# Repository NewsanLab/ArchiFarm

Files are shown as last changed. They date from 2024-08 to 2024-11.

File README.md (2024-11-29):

# 🌱 Proyecto de Cultivo en tu propio Smart Indoor
Este proyecto está diseñado para que cualquier persona pueda crear un sistema automatizado de cultivo indoor para lechugas. Usando tecnología accesible, hemos desarrollado un sistema que permite monitorear y optimizar el crecimiento de las plantas en interiores, subiendo los datos adquiridos a la plataforma Thingspeak para su análisis y seguimiento.
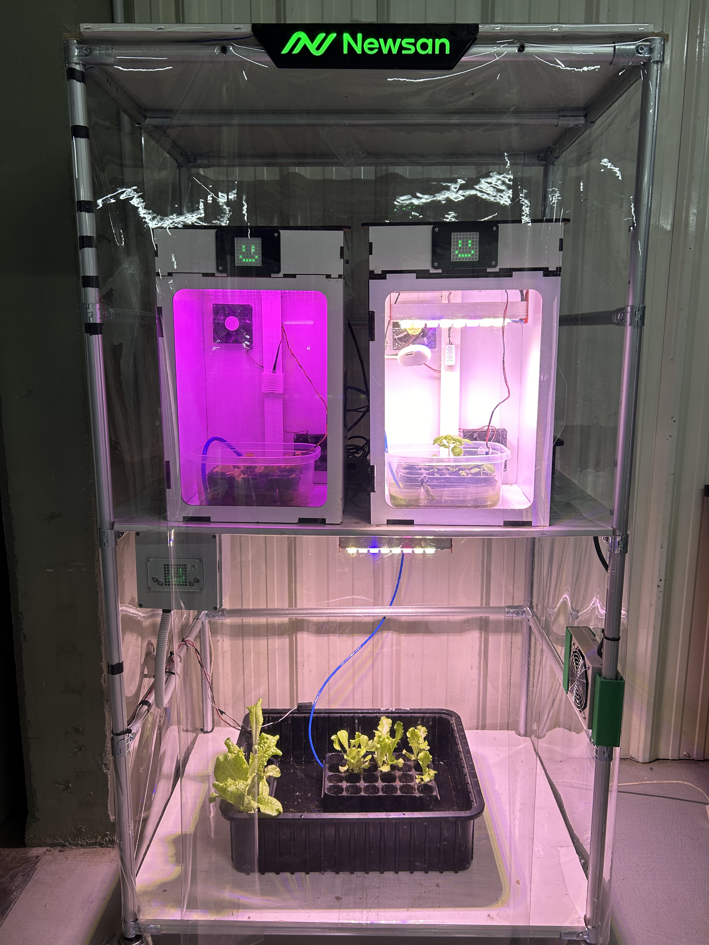
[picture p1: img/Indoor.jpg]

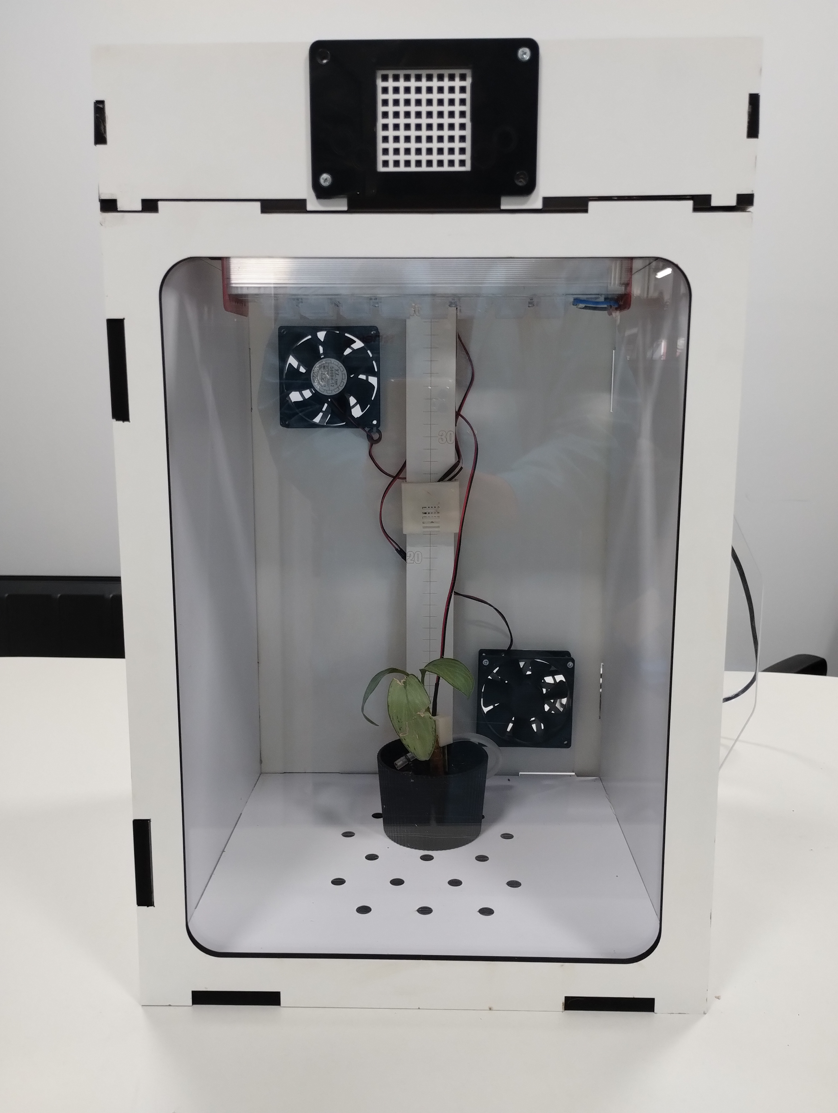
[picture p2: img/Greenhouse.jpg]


# 📖 Descripción
El proyecto de cultivo indoor de lechugas se centra en el desarrollo de un sistema inteligente que controla automáticamente las condiciones de crecimiento de las plantas. Este sistema incluye un conjunto de sensores y actuadores conectados a una placa de control diseñada específicamente para este propósito, llamada Archi Farm Beta. Con este sistema, es posible mantener las condiciones óptimas de luz, temperatura, humedad y riego para asegurar un crecimiento saludable de las lechugas.


# 🔧 Especificaciones Técnicas
- Placa Controladora: Archi Farm Beta, compatible con el microcontrolador Archi y Arduino Uno.
- Sensores Integrados: Sensor de humedad de suelo, sensor de temperatura y humedad ambiental.
- Actuadores: Luces LED Full Spectrum HPR16BOSV1, bomba de agua sumergible 600L/H 8W, coolers 220V AC.
- Alimentación: 220V AC para los actuadores principales y 5V DC para la placa de control y sensores.
- Conectividad: Capacidad de subir datos a Thingspeak mediante conexión Wi-Fi.
- Relés de Estado Sólido: Control de actuadores mediante salidas de relés.

# ⚙️ Esquema de Conexiones
A continuación se presenta el esquema de conexiones del sistema. Este esquema muestra cómo se conectan los sensores, actuadores y la placa controladora Archi Farm Beta.
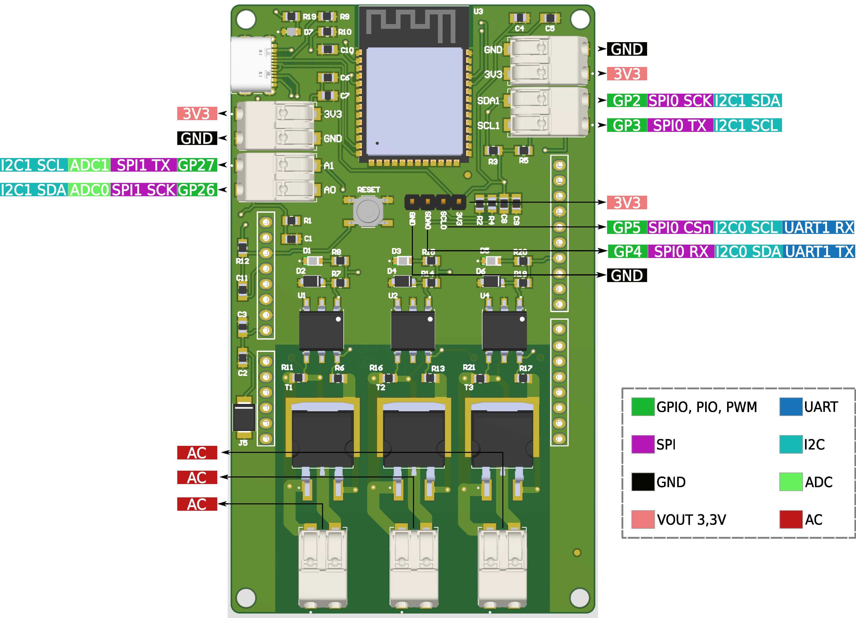
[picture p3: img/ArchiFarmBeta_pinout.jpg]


# 📜 Historia del Proyecto
El proyecto comenzó con la idea de desarrollar un método eficiente y controlado para cultivar lechugas en interiores, especialmente en áreas urbanas donde el espacio y las condiciones climáticas pueden ser limitantes. Tras varias iteraciones, logramos optimizar un sistema que no solo regula el ambiente de las plantas, sino que también permite subir los datos en tiempo real a una plataforma en la nube. De esta manera, cualquier persona puede monitorear y ajustar las condiciones de su cultivo desde cualquier lugar.

La primera versión del sistema utilizaba un método más simple para controlar la humedad y la luz, pero con el tiempo, se incorporaron tecnologías más avanzadas como la conexión a internet y el uso de la placa Archi Farm Beta, que mejoraron significativamente el rendimiento y la eficiencia del cultivo.

# 🗒 Historial de Cambios
v1.0: Primera versión del sistema, basada en un control manual de luces, riego y ventilacion. Tambien incluye conectividad a internet y puertos libre de proposito general.

# 🔗 Links Útiles
- [Archi](https://archikids.com.ar/)
- [Thingspeak](https://thingspeak.com/)

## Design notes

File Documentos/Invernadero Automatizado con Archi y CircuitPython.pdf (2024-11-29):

Invernadero Automatizado con Archi y CircuitPython ¡Bienvenidos al emocionante mundo de la automatización de invernaderos con tecnología! En este proyecto, exploramos cómo construir un invernadero automatizado que utiliza el potente microcontrolador Archi y el versátil entorno de programación CircuitPython. Este invernadero inteligente es capaz de monitorear y controlar las condiciones ambientales para garantizar el crecimiento saludable de las plantas.
Características del Proyecto:

Componentes:

Funcionamiento:

1. Control de Luz LED de Espectro Completo: Una luz LED de espectro completo proporciona a las plantas la iluminación adecuada para su crecimiento.
2. Riego Automático: Una bomba de agua automatizada se encarga de regar las plantas en el momento adecuado.
3. Regulación de Temperatura: Dos ventiladores (coolers) mantienen la temperatura dentro del invernadero en niveles óptimos.

Microcontrolador Archi
Placa de desarrollo Archi Farm Beta
Fuente de Alimentación 5V
SHT30: Sensor de Humedad y Temperatura del Ambiente Sensor Capacitivo de Humedad de Suelo (CSMS)
RTC (real time clock) DS3231
2 ventiladores “cooler” de 220v
Bomba de agua sumergible 220v
Luz LED Full Spectrum 220v
1. Los sensores SHT30 y CSMS están colocados en una carcasa impresa en 3D. El sensor SHT30 está conectado a los GP4 (I2C0 SDA) y GP5 (I2C0 SCL) de Archi, mientras que el CSMS está conectado al pin A0.
2. El microcontrolador Archi contiene una matriz led y botones (entre otras cosas). Dichos botones son usados para mostrar por pantalla los datos de humedad de ambiente, temperatura y humedad de suelo porcentual.
3. Se utiliza también un RTC el cual tiene la hora guardada, de manera de controlar la luz durante un rango de hora desde inicio hasta apagado. El RTC usa una pila cr2032 la cual permite guardar los datos de segundos, minutos,

Además, cuenta con un ESP32 S3 WROOM 1 el cual recibe los datos desde Archi y los publica en Thingspeak. Para la conexión se usaron los pines GP16 (UART0 TX) y GP17 (UART0 RX). La comunicación UART permite el envío y recepción de datos entre Archi y ESP32. Para la programación de la ESP32 se conecta usb tipo c en el conector al lado del Esp32

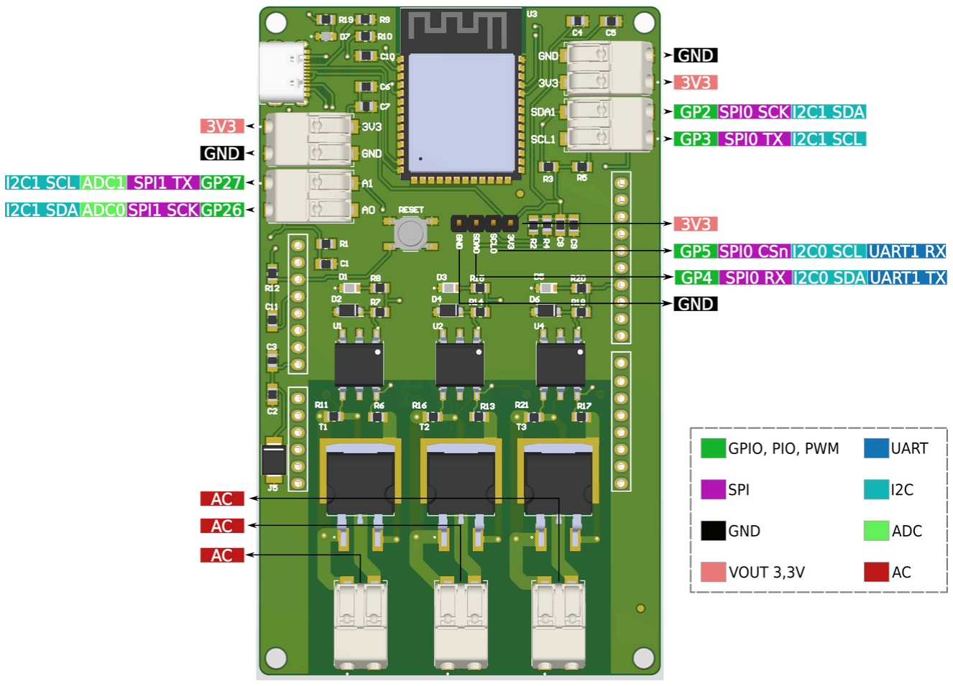
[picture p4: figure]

Finalmente, conectamos a nuestra pc y programamos el archivo “Code_ESP32_WROOM1” usando el Arduino IDE.
No olvides introducir en nombre de la red wifi, contraseña y la API de Thingspeak en código de la ESP32, de contrario no funcionará.
Instrucciones:

hora, día, mes y año. El RTC está conectados a los pines GP2 (I2C1 SDA) y GP3 (I2C1 SCL) de Archi, pero puedes usar los mismos pines que el sensor SHT30.
4. La placa de desarrollo Archi Farm Beta contiene 3 relés de estado sólido para controlar actuadores de 220v de AC. También cuenta con leds que se encienden y apagan junto con cada relé. Cada relé está conectado con los pines GP13, GP14 y GP15.
1. Clona o descarga este repositorio en tu computadora.
2. Configura el entorno de desarrollo para el microcontrolador Archi y CircuitPython siguiendo las instrucciones proporcionadas en el README.

Imágenes y Esquemas:
Puedes encontrar imágenes del invernadero y de los componentes en la carpeta "img" de este repositorio.
Notas de Seguridad:

¡Ahora estás listo para sumergirte en el emocionante proyecto de tu invernadero automatizado con Archi y CircuitPython! Recuerda, este tutorial está diseñado para ser amigable para los principiantes y está pensado para inspirar el aprendizaje y la exploración. ¡Diviértete y disfruta del proceso de construcción y aprendizaje!

3. Ve a https://archikids.com.ar y presiona el boton Code Editor.
4. Carga el código en el Archi usando el archivo de código fuente en formato CircuitPython (code.py). No olvides cargar las librerías en la carpeta lib.
5. Coloca los sensores en la carcasa impresa y posiciónalos en el invernadero.
6. Conecta los dispositivos controlados (ventiladores, bomba, luz) al módulo de relés.
7. Conecta la fuente de alimentación y enciende el invernadero automatizado.

Al tratar con dispositivos eléctricos de alto voltaje, asegúrate de tomar todas las precauciones de seguridad necesarias.
Mantén el invernadero en un lugar seguro y bien ventilado.

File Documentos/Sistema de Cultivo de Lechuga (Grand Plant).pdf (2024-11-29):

Sistema de Cultivo de Lechuga (Grand Plant) Materiales Utilizados:

Como hacer un Plantín:
Para preparar el sustrato, primero es necesario humedecerlo y removerlo bien. Esto asegura que el aire circule dentro de la tierra, lo que es esencial para el desarrollo de las raíces. Una vez listo, se coloca el sustrato en los speedlings, dejando unos 5mm libres en la parte superior para colocar las semillas. Debes poner dos semillas en cada hueco y luego cubrirlas con una fina capa de tierra. Es fundamental rociar agua para mantener la humedad constante en el sustrato. Una vez que el speedling esté listo, se debe colocar en un recipiente con agua previamente preparada con soluciones hidropónicas. La preparación del agua dependerá de las instrucciones de cada nutriente que utilices. Ahora, coloca el sensor de humedad de suelo en la tierra para monitorear la humedad de manera constante.
Durante nuestros primeros ensayos, cubrimos los semilleros con una bolsa de plástico para aumentar la humedad. Sin embargo, la luz que llegaba a los plantines hacía que se estiraran demasiado, lo que no es beneficioso para el cultivo de lechugas. Luego, descubrimos que era mejor privar a los plantines de luz en esta etapa inicial, aunque el crecimiento seguía siendo algo lento.

Luz HPR16BOSV1 con disipador Ventiladores 220V AC
Bomba de Agua Sumergible 600L/H 8W Sustrato
Speedlings (bandejas para germinación)
Recipiente
Nutrientes para hidroponía Minamot: ROOTDROP, FULLDROP A y FULLDROP B

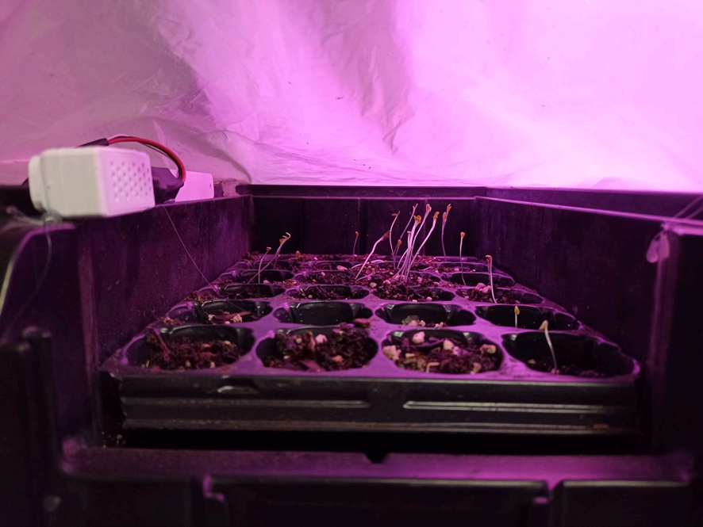
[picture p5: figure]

Posteriormente, decidimos colocar los plantines desde el primer día en un indoor equipado con luces HPR16BOSV1. Aunque la humedad ambiental no era tan alta como en el experimento anterior, estas luces, que incluyen diferentes tipos de LEDs, permitieron un crecimiento más equilibrado de los plantines. Es importante mencionar que mantuvimos una distancia de 25 cm entre las luces y los plantines. Esta distancia es crucial, ya que si las luces están demasiado lejos, las lechugas tienden a estirarse, lo que no es ideal para su desarrollo.
Condiciones del Ensayo (para Lechugas):

18 horas de luz por día
Rango de temperaturas entre 18°C y 28°C
Humedad ambiental mayor al 40%

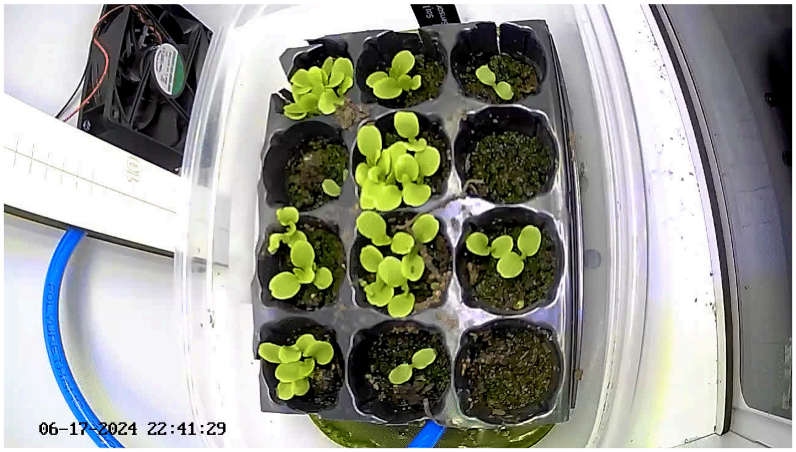
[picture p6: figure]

Después de dos o tres semanas, es necesario trasladar los plantines a un espacio más grande y aumentar la distancia entre las luces y las plantas a aproximadamente 1 metro. Este cambio es vital para que las plantas sigan creciendo de manera adecuada. Si las plantas permanecen en un espacio pequeño y con la luz demasiado cerca, su crecimiento se verá limitado.
En la imagen, se pueden ver lechugas de distintos tamaños. Las lechugas más grandes fueron trasladadas a un espacio más amplio una semana antes, lo que les permitió crecer más rápidamente. Por otro lado, las plantas más pequeñas permanecieron en el espacio reducido durante esa semana adicional, lo que limitó su crecimiento.

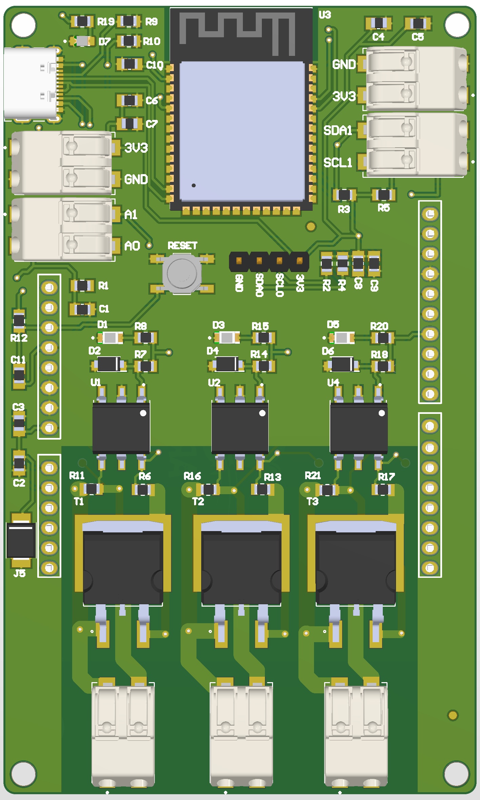
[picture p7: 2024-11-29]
Hardware/Archi_Farm_Beta.jpg

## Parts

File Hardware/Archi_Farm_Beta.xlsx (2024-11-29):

PartType | Description | Value | Designator | Package | Quantity
CC0805JPNPO9BN102 | CAP CER 1000PF 50V C0G/NPO 2012M | 1000pF | C11 | 2012M | 1
CRCW0805270RFKEAC | 270 Ohms ±1% 0.125W, 1/8W Chip Resistor 2012M | 270ohms | R8, R15, R19, R20 | 2012M | 4
CRCW0805220RFKEBC | 220 Ohms ±1% 0.125W, 1/8W Chip Resistor 2012M | 220ohms | R6, R7, R13, R14, R17, R18 | 2012M | 6
CRCW080556R0FKEAC | 56 Ohms ±1% 0.125W, 1/8W Chip Resistor 2012M | 56ohms | R11, R16, R21 | 2012M | 3
CC0805JPNPO9BN470 | 47 pF ±5% 50V Ceramic Capacitor C0G, NP0 2012M | 47pF | C1 | 2012M | 1
CC0805ZKY5V5BB106 | CAP CER 10UF 6.3V Y5V 2012M | 10uF | C2, C4, C6, C8, C10 | 2012M | 5
CRCW080510K0FKEA | 10 kOhms ±1% 0.125W, 1/8W Chip Resistor 2012M | 10kohms | R2, R3, R4, R5 | 2012M | 4
CRCW08055K00JNTA | 5 kOhms ±5% 0.125W, 1/8W Chip Resistor 2012M | 5kohms | R9, R10 | 2012M | 2
CRCW08051K00FKEA | RES SMD 1K OHM 1% 1/8W 2012M | 1kohms | R1, R12 | 2012M | 2
CC0805KRX7R9BB104 | CAP CER 0.1UF 50V X7R 2012M | 0.1uF | C3, C5, C7, C9 | 2012M | 4
1N4007W-T | DIODE GEN PURP 1KV 1A SOD-123FL |  | D2, D4, D6 | SOD-123FL | 3
2060-452_998-404 | 2 Position Wire to Board Terminal Block Horizontal with Board 0.157 (4.00mm) Surface Mount |  | J1, P0, P1, P2, P3, P4, P5 | 2 Position Wire to Board Terminal Block Horizontal with Board 0.157" (4.00mm) Surface Mount | 7
2171790001 | USB-C (USB TYPE-C) USB 2.0 Receptacle Connector 24 (16+8 Dummy) Position Surface Mount, Right Angle; Through Hole |  | J3 | USB-C (USB TYPE-C) USB 2.0 Receptacle Connector 24 (16+8 Dummy) Position Surface Mount, Right Angle; Through Hole | 1
5990110007F | Red 633nm LED Indication - Discrete 2.1V 2012M |  | D1, D3, D5, D7 | 2012M | 4
61300411121 | Connector Header Through Hole 4 position 0.100 (2.54mm) |  | J2 | Connector Header Through Hole 4 position 0.100 (2.54mm) | 1
ESP32-S3-WROOM-1-N8 | WiFi 802.11a/b/g/n, Bluetooth v5.0 Transceiver Module 2.4GHz PCB Trace |  | U3 | ESP32-S3-WROOM-1-N8 | 1
MOC3041XSM | OPTOISOLATOR 5.3KV TRIAC 6SMD |  | U1, U2, U4 | 6SMD | 3
SMBJ5.0CA | 9.2V Clamp 65.2A Ipp Tvs Diode Surface Mount DO-214AA (SMB) |  | J5 | DO-214AA | 1
T1635-800G-TR | TRIAC ALTERNISTOR 800V 16A D2PAK |  | T1, T2, T3 | D2PAK | 3
TL3342F160QG | SWITCH TACTILE SPST-NO 0.05A 12V |  | S1 | Outline 4.90mm x 4.90mm | 1
ARCHI_SHIELD |  |  | A1 |  | 1

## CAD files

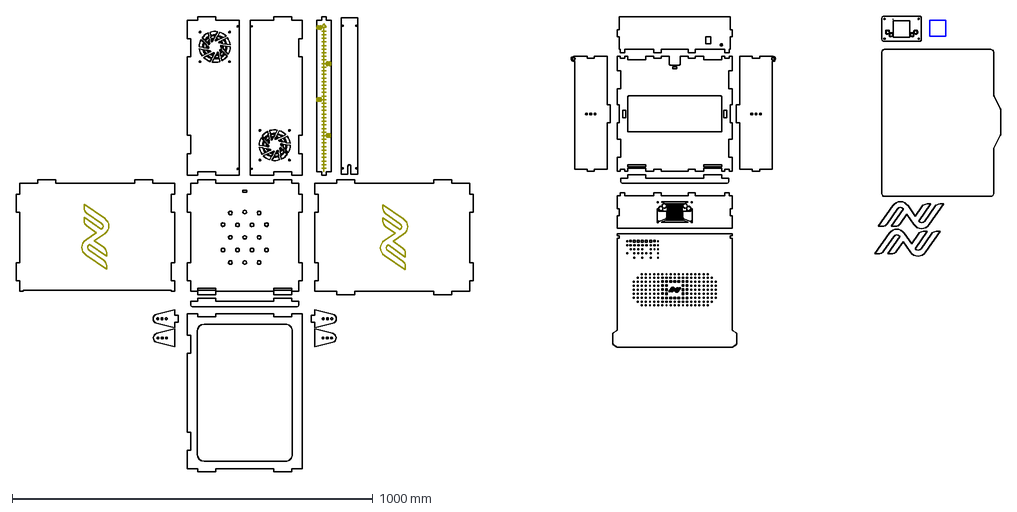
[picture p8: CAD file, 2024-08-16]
Diseño/Indoor archikids newsan.dxf
2727.3 x 1262.5 mm

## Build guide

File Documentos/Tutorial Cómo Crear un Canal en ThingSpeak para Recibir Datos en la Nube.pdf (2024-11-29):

Tutorial: Cómo Crear un Canal en ThingSpeak para Recibir Datos en la Nube ¡Hola! Hoy vamos a aprender a crear un canal en ThingSpeak para recibir datos desde un microcontrolador. ThingSpeak es una plataforma en la nube que te permite almacenar y visualizar datos en tiempo real. Es perfecta para proyectos como estaciones meteorológicas, monitoreo de sensores, y más.
¿Qué Necesitas?

Paso 1: Crear una Cuenta en ThingSpeak

Paso 2: Crear un Nuevo Canal

Una computadora con acceso a Internet.
Una cuenta gratuita en ThingSpeak.
Un microcontrolador (ESP8266, ESP32, etc.) conectado a Internet.
1. Abre tu navegador web y visita www.thingspeak.com.
2. Haz clic en "Sign Up" o "Crear cuenta".
3. Completa el formulario de registro con tu correo electrónico y una contraseña. Luego, sigue las instrucciones para verificar tu cuenta.

Una vez que hayas iniciado sesión, haz clic en "New Channel ".

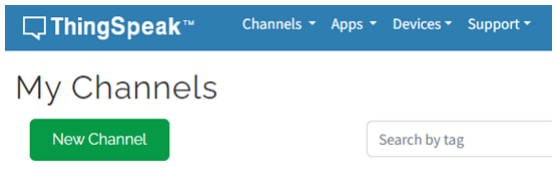
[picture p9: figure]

Aparecerá un formulario donde deberás ingresar los detalles de tu canal: Name (Nombre): Pon un nombre descriptivo para tu canal, por ejemplo, "Monitoreo de Temperatura".
Description (Descripción): Añade una breve descripción de lo que hará tu canal, como "Este canal recibe datos de temperatura desde un sensor". Fields (Campos): Marca las casillas de los campos que vas a utilizar (puedes tener hasta 8 campos). Un campo podría ser "Temperatura", otro "Humedad", etc.

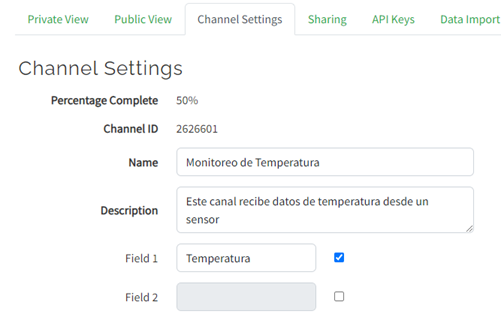
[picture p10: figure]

Paso 3: Obtener la API Key
La API Key es una clave única que permite que tu microcontrolador envíe datos a tu canal en ThingSpeak.

Paso 4: Configurar el Código en el Microcontrolador
Ahora que tienes la API Key, necesitas programar tu microcontrolador para enviar datos a ThingSpeak.
Paso 5: Ver los Datos en ThingSpeak

Haz clic en "Save Channel" o "Guardar Canal". ¡Felicidades! Has creado tu primer canal en ThingSpeak.

1. Ve a la pestaña "API Keys" en tu canal recién creado.
2. Aquí verás dos claves: "Write API Key" y "Read API Key".
La "Write API Key" es la que necesitas para enviar datos a ThingSpeak desde tu microcontrolador.
3. Copia la "Write API Key". La utilizarás en tu código para permitir que tu microcontrolador se comunique con ThingSpeak.
1. Vuelve a tu canal en ThingSpeak.
2. En la pestaña "Private View" o "Vista Privada", podrás ver las gráficas de los datos que estás enviando desde tu microcontrolador.
3. Si todo está funcionando correctamente, verás cómo los datos se actualizan en tiempo real.

¡Listo!

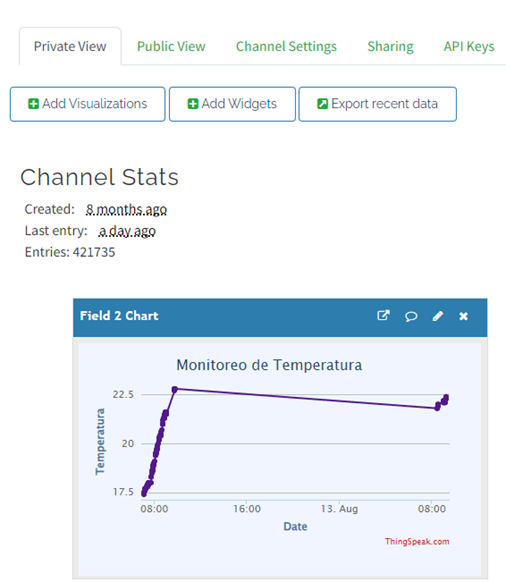
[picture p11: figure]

Has aprendido cómo crear un canal en ThingSpeak y cómo enviar datos desde un microcontrolador. ¡Ahora puedes monitorizar cualquier cosa que se te ocurra desde cualquier lugar del mundo!

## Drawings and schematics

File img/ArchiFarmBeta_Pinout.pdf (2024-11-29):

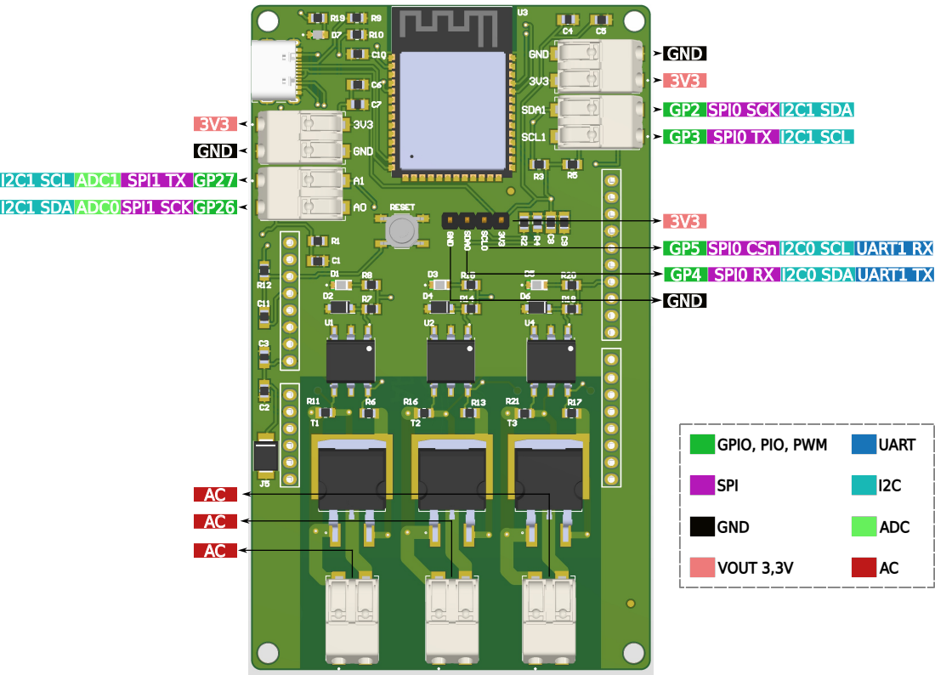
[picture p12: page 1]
GND; I2C1 SCL ADC1 SPI1 TX GP27 I2C1 SDA ADC0 SPI1 SCK GP26; GND 3V3; GP2 SPI0 SCK I2C1 SDA GP3 SPI0 TX I2C1 SCL; 3V3 GP5 SPI0 CSn I2C0 SCL GP4 SPI0 RX I2C0 SDA; UART1 RX UART1 TX; SPI; ADC; UART; VOUT 3,3V

GPIO, PIO, PWM

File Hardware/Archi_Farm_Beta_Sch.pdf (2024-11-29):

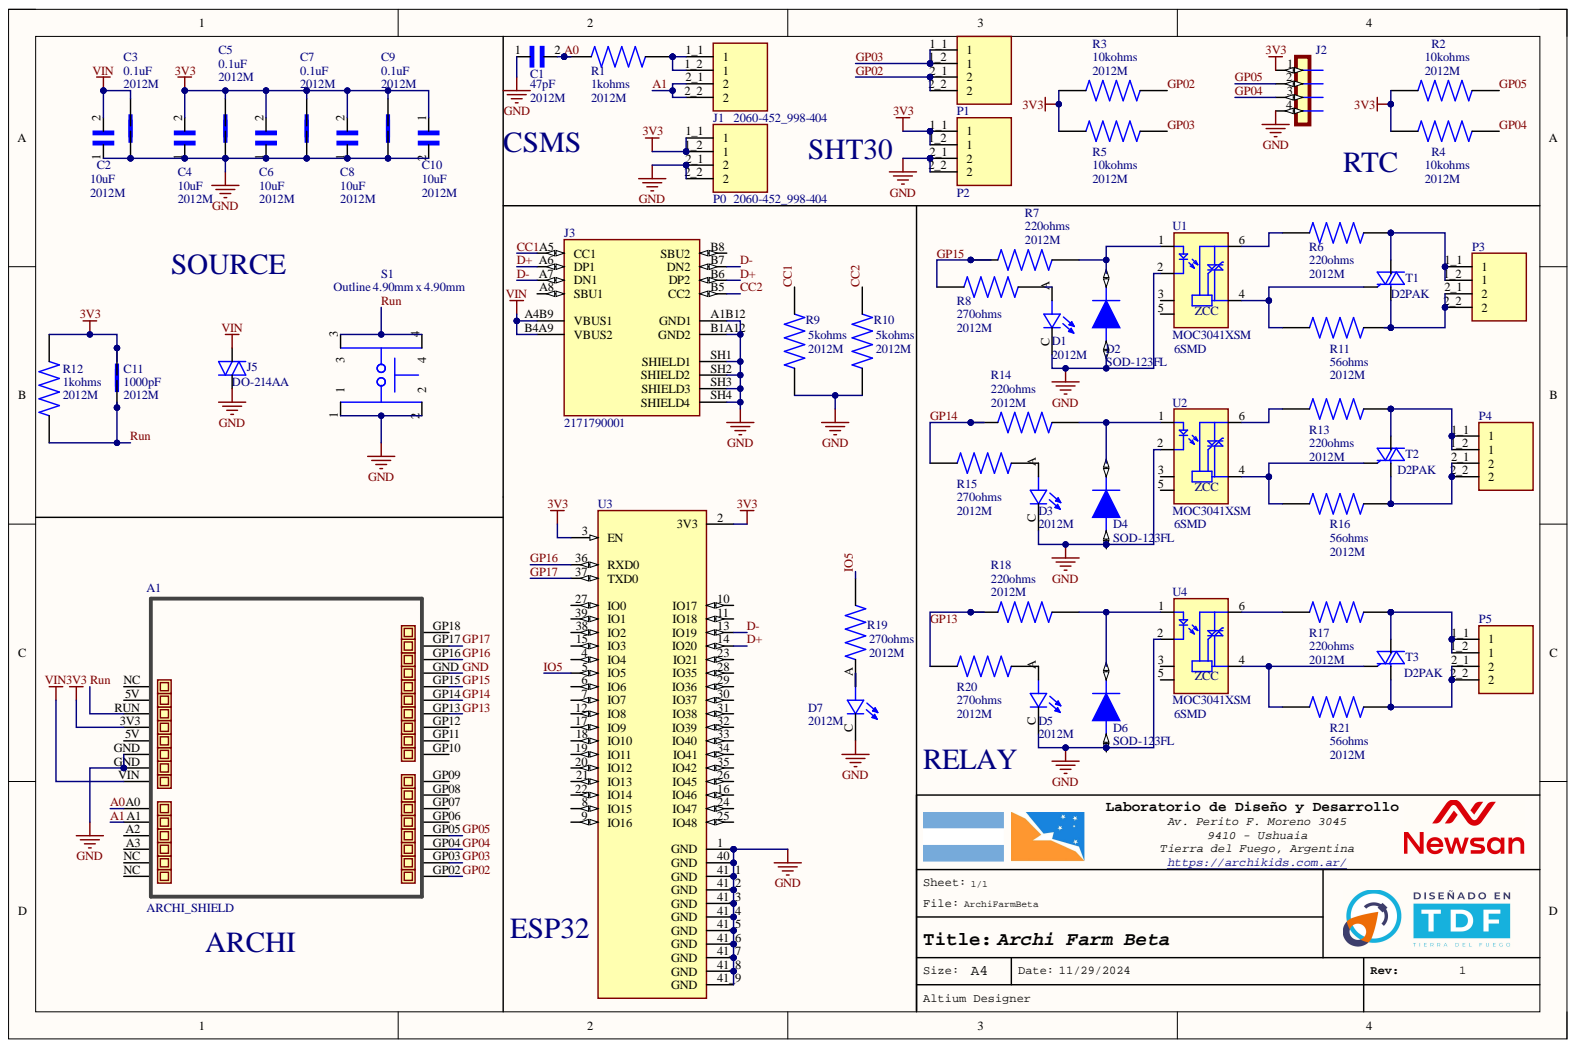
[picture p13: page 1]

UN5VNC

ño y Desarrollo Av. Perito F. Moreno 3045

Tierra del Fuego, Argentina
https://archikids.com.ar/

Size: A4 | Date: 11/29/2024 | Rev: 1

Altium Designer

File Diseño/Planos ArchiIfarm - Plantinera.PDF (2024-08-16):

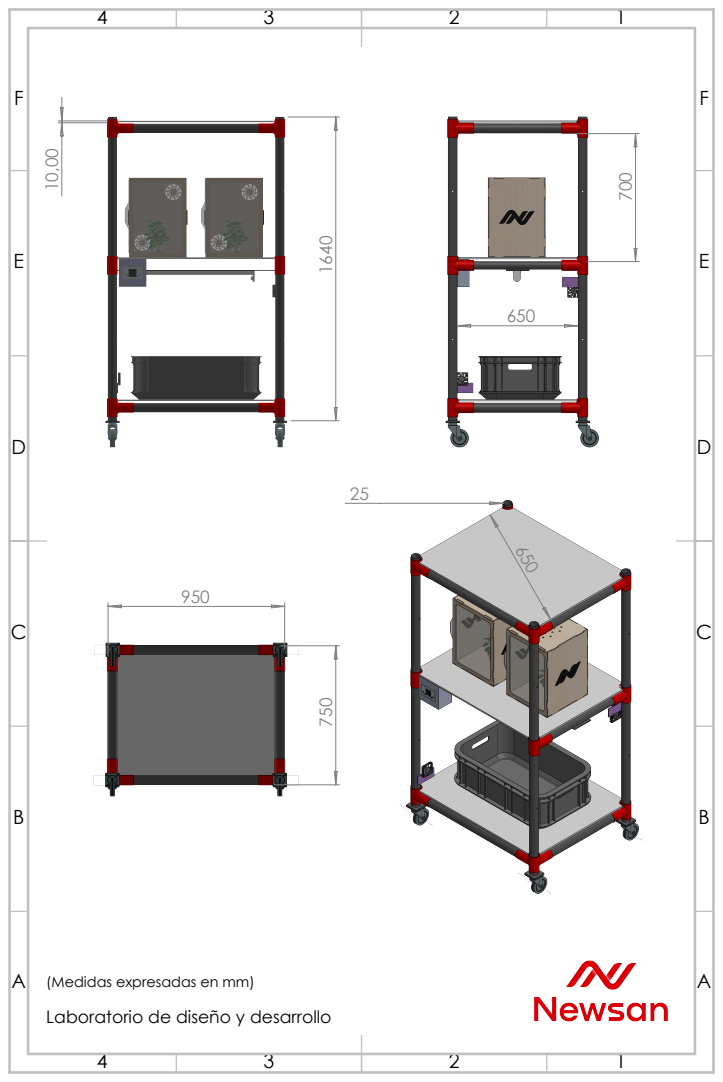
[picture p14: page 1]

(Medidas expresadas en mm)
Laboratorio de diseño y desarrollo

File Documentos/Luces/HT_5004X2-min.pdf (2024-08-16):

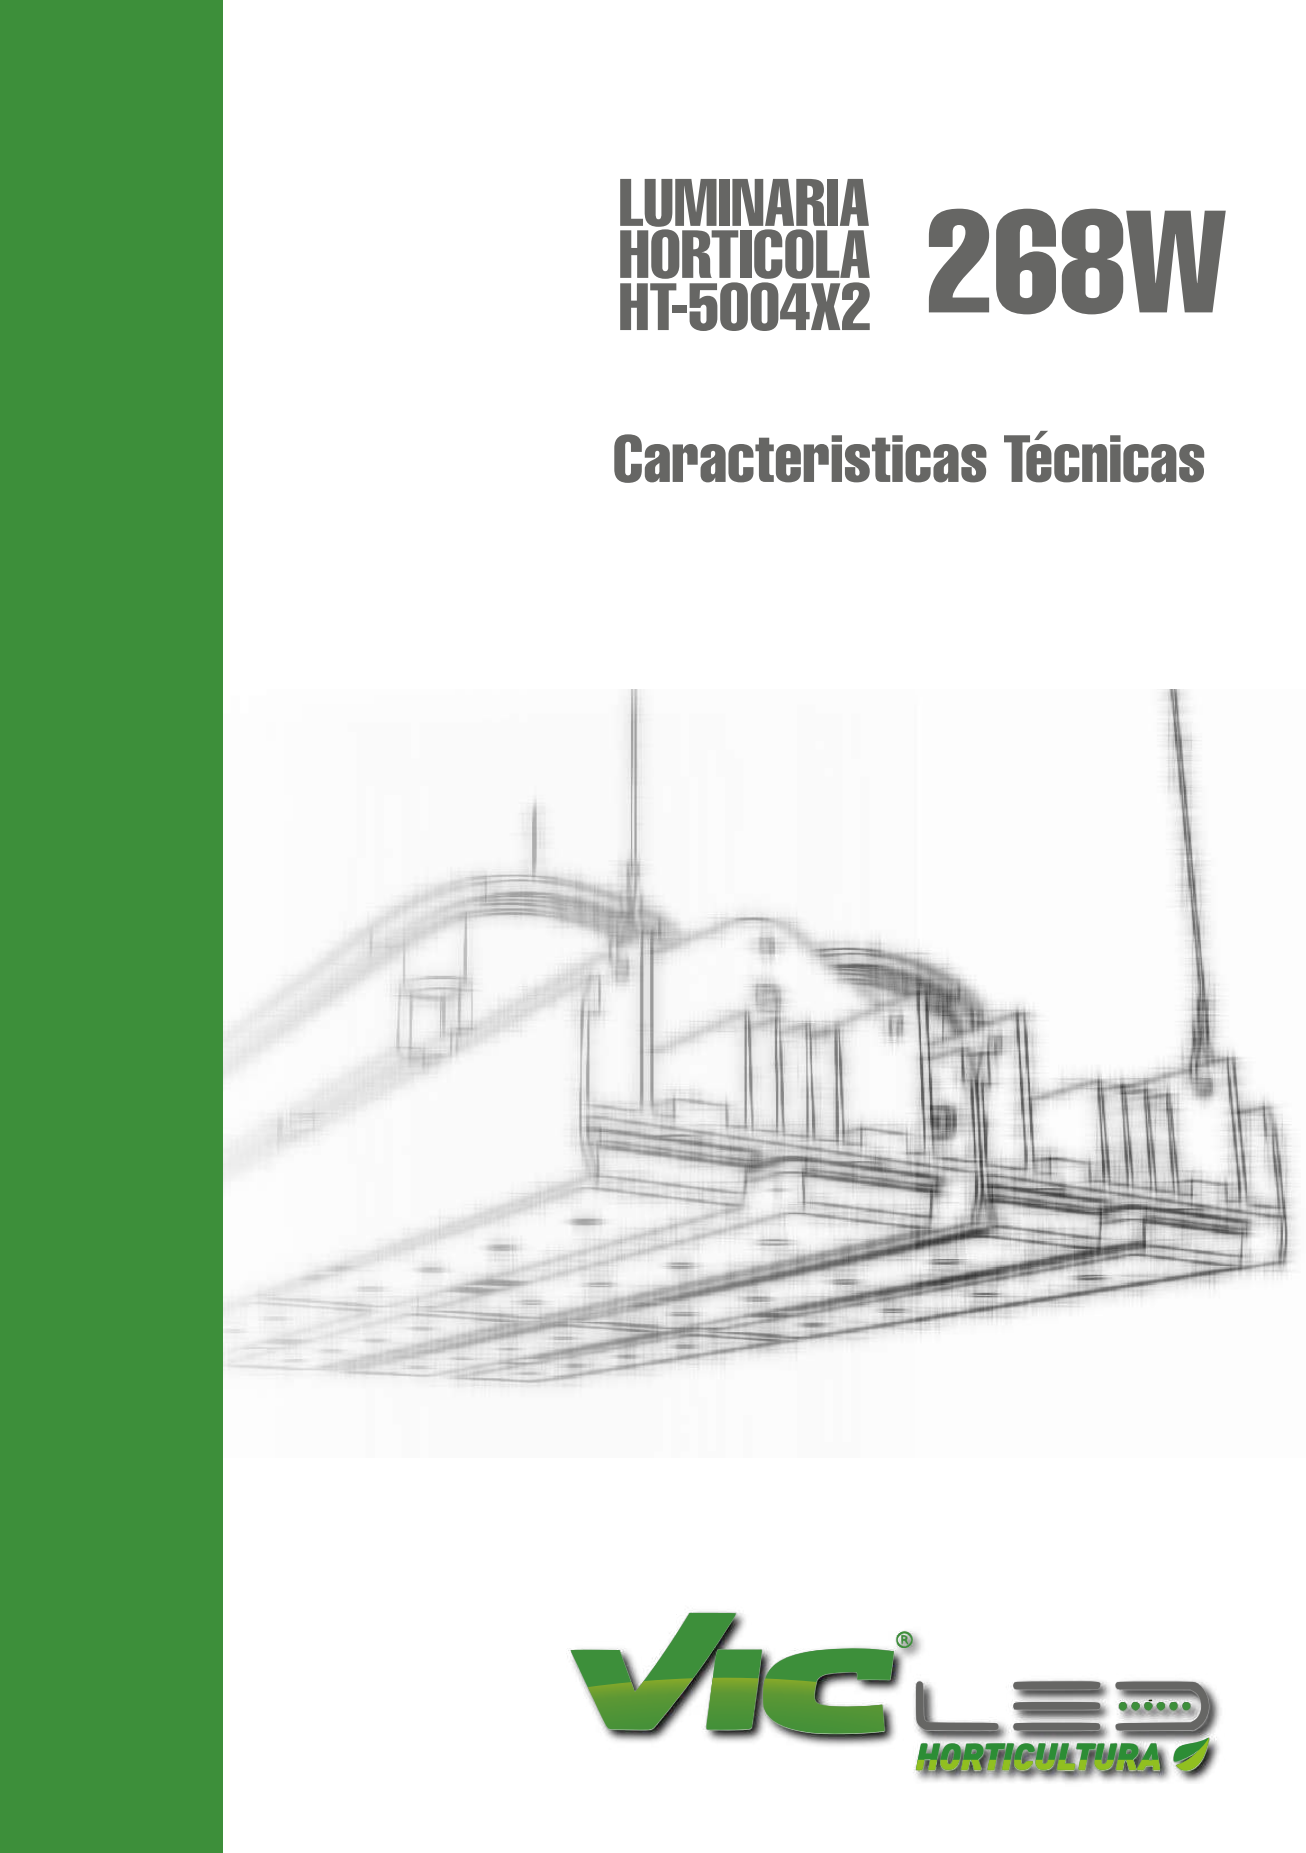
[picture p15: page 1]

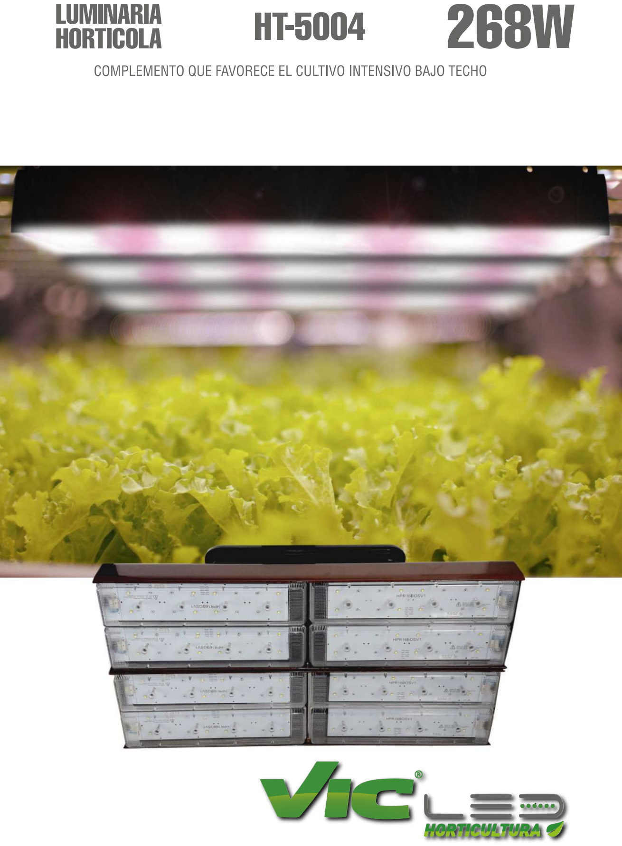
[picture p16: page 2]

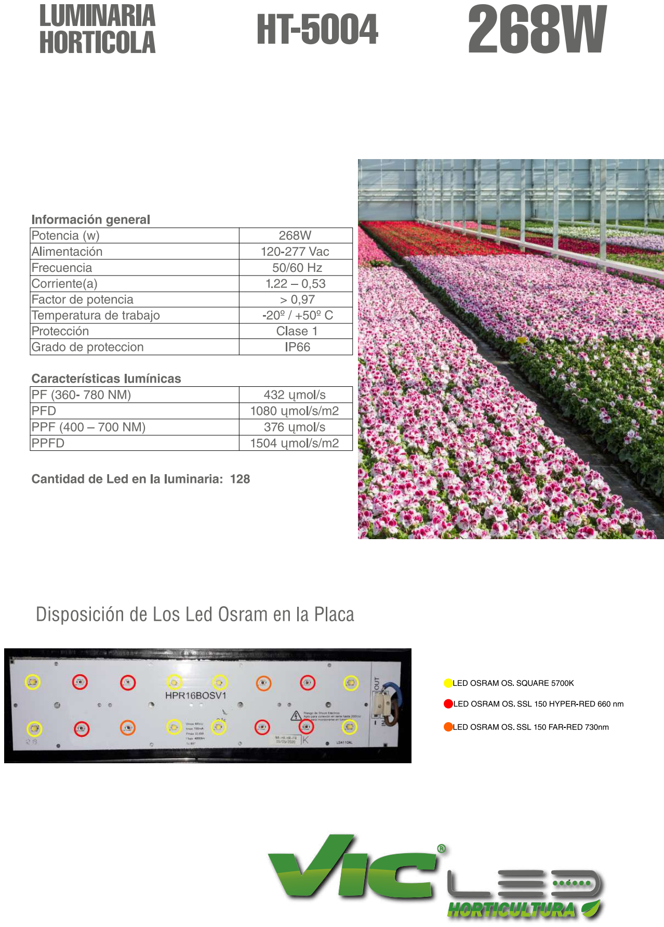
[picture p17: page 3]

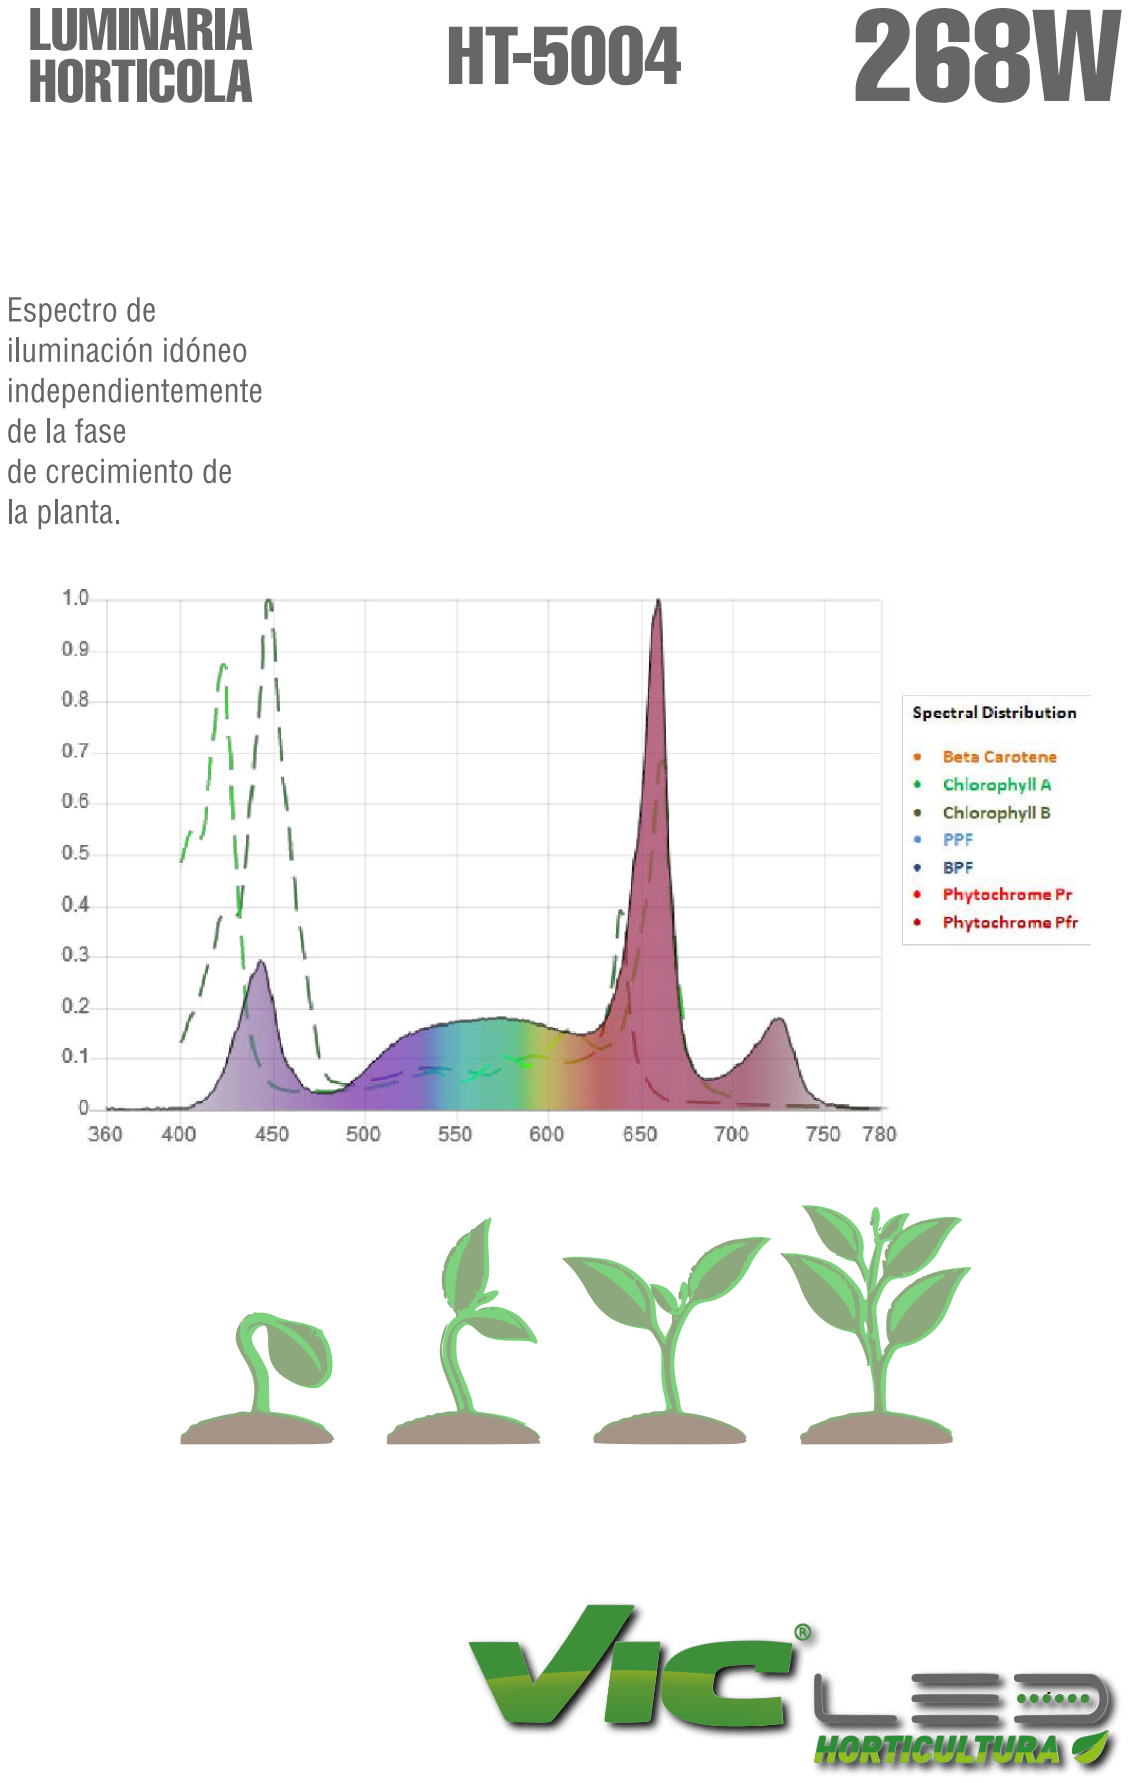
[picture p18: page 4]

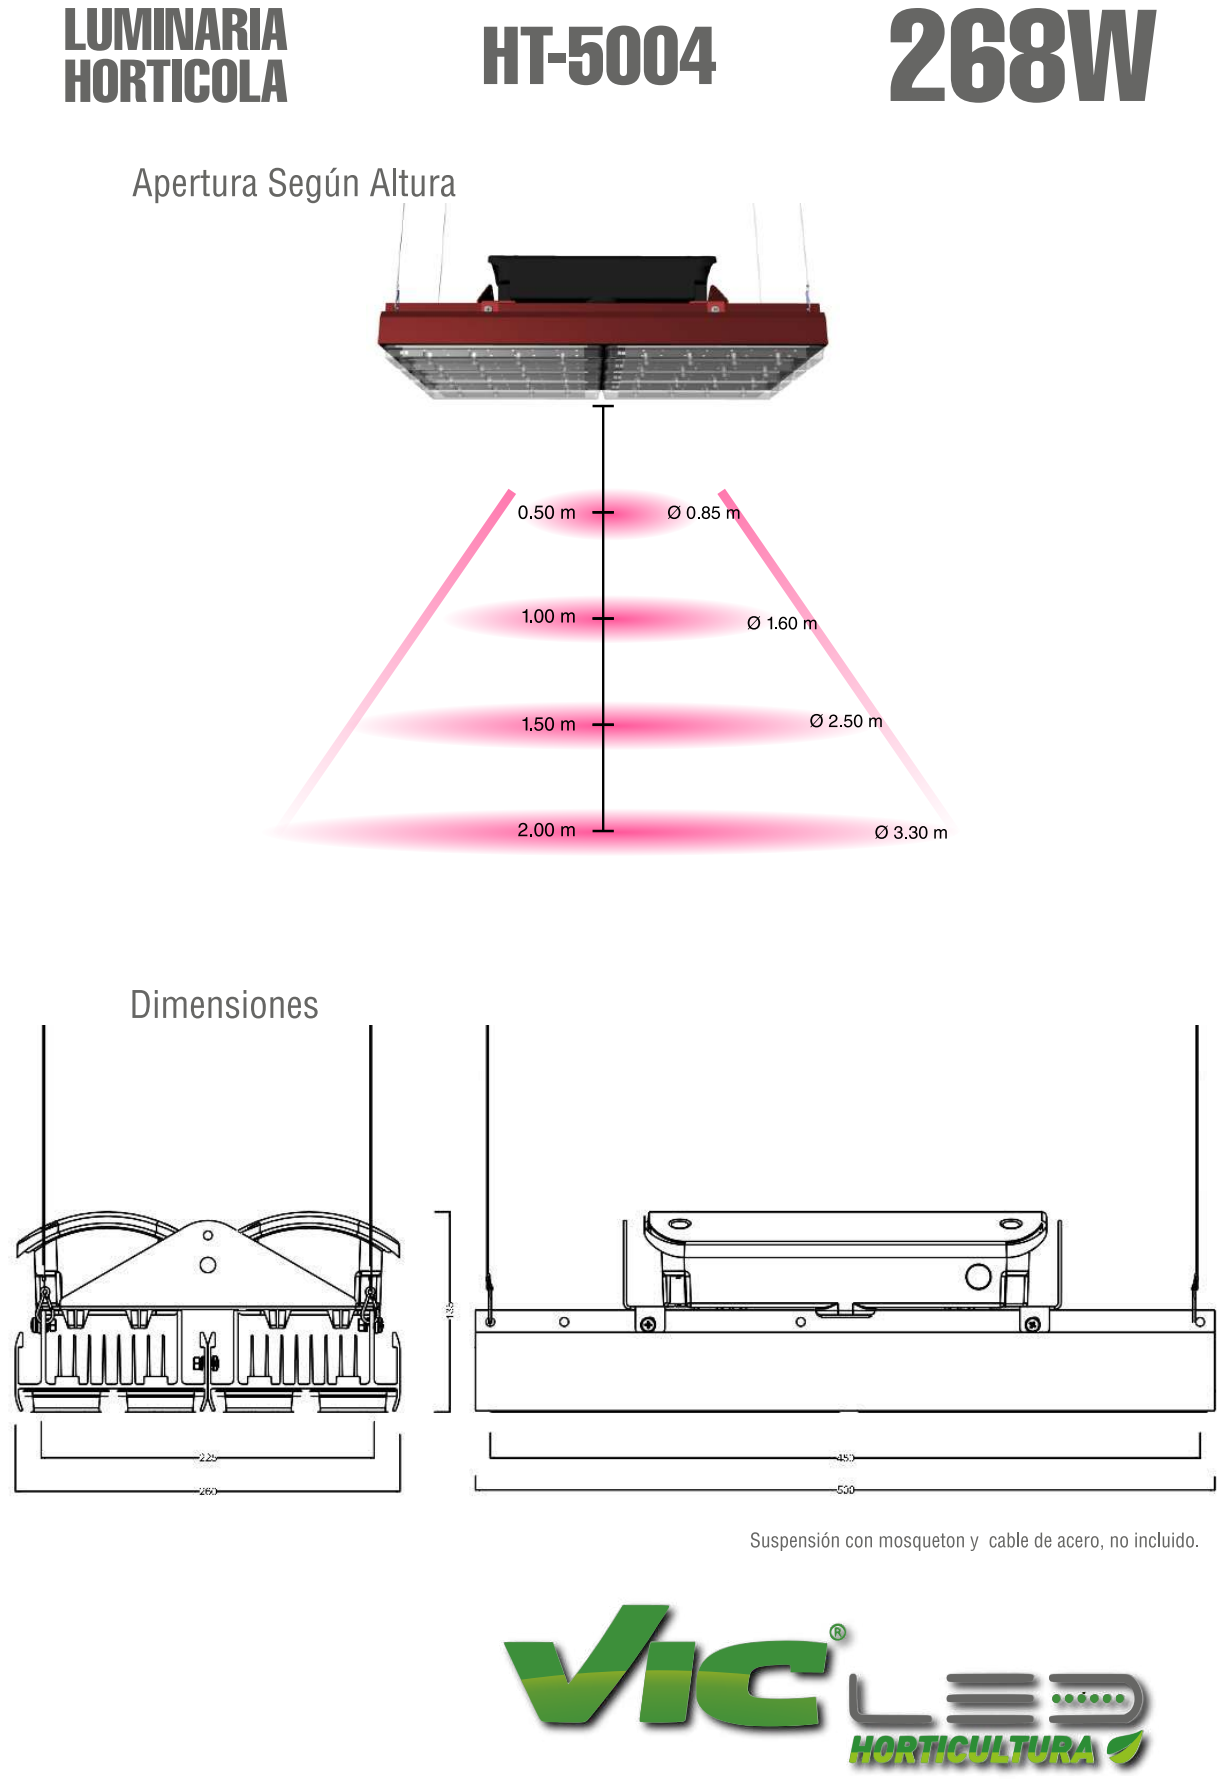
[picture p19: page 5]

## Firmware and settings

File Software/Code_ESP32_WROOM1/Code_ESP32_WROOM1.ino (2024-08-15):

// Librerias
#include <WiFi.h>
//#include <ESP8266WiFi.h>

// Configuración de la red WiFi
const char *ssid = "";// Ingresa el nombre de tu red Wi-Fi
const char *password = "";// Ingresa la contrasena de tu Wi-Fi

// Configuración ThingSpeak
const char *thingSpeakAddress = "api.thingspeak.com";
const String writeAPIKey = "";//Ingresa la API de tu canal en Thinkspeak

const char *DEVICE_LABEL = "Esp32";// ingresa el nombre de tu Dispositivo Esp32
String temperature = "temperatura";// Ingresa el nombre de la variable que quieres publicar en Thinkspeak
String humidity = "humedad-ambiente";// Ingresa el nombre de la variable que quieres publicar en Thinkspeak
String soil_humidity = "humedad-suelo";// Ingresa el nombre de la variable que quieres publicar en Thinkspeak

void callback(char *topic, byte *payload, unsigned int length)
{
  Serial.print("Message arrived [");
  Serial.print(topic);
  Serial.print("] ");
  for (int i = 0; i < length; i++)
  {
    Serial.print((char)payload[i]);
  }
  Serial.println();
}

void setup()
{

  // Ingresa tu codigo que solo correra una vez al iniciar
  Serial.begin(115200);

  // Inicia la conexcion a internet
  WiFi.begin(ssid, password);
  while (WiFi.status() != WL_CONNECTED) {
    delay(1000);
    Serial.println("Connecting to WiFi...");
  }
  Serial.println("Connected to WiFi");
}

void loop()
{
  if (Serial.available() > 0) {
      String topic = "";
      // Se reciben los datos desde Archi
      while (Serial.available() > 0){
        char dato = Serial.read();
        topic = topic + dato;
      }
      // Se procesa los datos recibidos
      if (topic[0] == 'T'){
        temperature = topic.substring(1);// Ingresa tu variable y el valor medido
        // Envío de datos a ThingSpeak
        String data = "field2=" + String(temperature);
        if (sendDataToThingSpeak(data)) {
         Serial.println("Dato enviado a ThingSpeak!");
         }   
        else{
          Serial.println("Fallo el envio de Dato a ThingSpeak");} 
      }

      if (topic[0] == 'A'){
        humidity = topic.substring(1);// Ingresa tu variable y el valor medido
        // Envío de datos a ThingSpeak
        String data = "field1=" + String(humidity);
        if (sendDataToThingSpeak(data)) {
         Serial.println("Dato enviado a ThingSpeak!");
         }   
        else{
          Serial.println("Fallo el envio de Dato a ThingSpeak");}      
        }

      if (topic[0] == 'S'){
        soil_humidity = topic.substring(1);// Ingresa tu variable y el valor medido
        // Envío de datos a ThingSpeak
        String data = "field3=" + String(soil_humidity);
        if (sendDataToThingSpeak(data)) {
         Serial.println("Dato enviado a ThingSpeak!");
         }   
        else{
          Serial.println("Fallo el envio de Dato a ThingSpeak");}       
      }
    }

    delay(1000);
  }

 bool sendDataToThingSpeak(String data) {
  WiFiClient client;
  if (!client.connect(thingSpeakAddress, 80)) {
    return false;
  }

  String request = "POST /update HTTP/1.1\n";
  request += "Host: " + String(thingSpeakAddress) + "\n";
  request += "Connection: close\n";
  request += "X-THINGSPEAKAPIKEY: " + writeAPIKey + "\n";
  request += "Content-Type: application/x-www-form-urlencoded\n";
  request += "Content-Length: " + String(data.length()) + "\n\n";
  request += data;

  client.print(request);

  delay(1000);

  client.stop();
  return true;
}

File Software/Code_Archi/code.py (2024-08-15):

# Escribe tu supercódigo aquí :-)
# Iniciamos declarando las librerias necesarias
import neopixel
from adafruit_pixel_framebuf import PixelFramebuffer
import board
import busio
import adafruit_ds3231
import adafruit_sht31d
from digitalio import DigitalInOut, Direction, Pull
import analogio
import digitalio
import time
import simpleio

# Definimos las variables
texto = None
color = None
valor = None
hora_inicio_luz = None
hora_apagado_luz = None
reloj = None
luz = None
porcentaje_humedad_suelo = None
limite_humedad_suelo_min = None
limite_humedad_suelo_max = None
bomba_agua = None
temperatura_ambiente = None
limite_temp_ambiente_max = None
limite_temp_ambiente_min = None
fan_cooler = None
limite_tem_ambiente_min = None
sensor_temp_humed_ambiente = None
humedad_suelo_min = None
humedad_suelo_max = None
sensor_humedad_suelo = None
humedad_ambiente = None
sensor_nivel_agua = None

# Declaramos una funcion para controlar la luz
def gestionar_estado_luz(hora_inicio_luz, hora_apagado_luz, hora_actual, luz):
    global texto, color, valor, porcentaje_humedad_suelo, limite_humedad_suelo_min, limite_humedad_suelo_max, bomba_agua_1, bomba_agua_2, bomba_agua_3, temperatura_ambiente, limite_temp_ambiente_max, limite_temp_ambiente_min, fan_cooler, limite_tem_ambiente_min, sensor_temp_humed_ambiente, humedad_suelo_min, humedad_suelo_max, sensor_humedad_suelo, humedad_ambiente

    if hora_inicio_luz < hora_apagado_luz:
        if (hora_inicio_luz <= hora_actual) and (
            hora_actual < hora_apagado_luz
        ):
            luz.value = True
        else:
            luz.value = False
    else:
        if (hora_inicio_luz <= hora_actual) or (
            hora_actual < hora_apagado_luz
        ):
            luz.value = True
        else:
            luz.value = False

# Declaramos una funcion para controlar la bomba
def gestionar_estado_bomba_agua(
    porcentaje_humedad_suelo,
    limite_humedad_suelo_min,
    limite_humedad_suelo_max,
    bomba_agua,
):
    global texto, color, valor, hora_inicio_luz, hora_apagado_luz, reloj, luz, temperatura_ambiente, limite_temp_ambiente_max, limite_temp_ambiente_min, fan_cooler, limite_tem_ambiente_min, sensor_temp_humed_ambiente, humedad_suelo_min, humedad_suelo_max, sensor_humedad_suelo, humedad_ambiente
    if porcentaje_humedad_suelo <= limite_humedad_suelo_min:
        bomba_agua.value = True
    elif porcentaje_humedad_suelo >= limite_humedad_suelo_max:
        bomba_agua.value = False

# Declaramos una funcion para controlar los coolers de entrada y salida de aire
def gestionar_estado_cooler(
    temperatura_ambiente, limite_temp_ambiente_max, limite_temp_ambiente_min, fan_cooler
):
    global texto, color, valor, hora_inicio_luz, hora_apagado_luz, reloj, luz, porcentaje_humedad_suelo, limite_humedad_suelo_min, limite_humedad_suelo_max, bomba_agua_1, bomba_agua_2, bomba_agua_3, limite_tem_ambiente_min, sensor_temp_humed_ambiente, humedad_suelo_min, humedad_suelo_max, sensor_humedad_suelo, humedad_ambiente
    if temperatura_ambiente >= limite_temp_ambiente_max:
        fan_cooler.value = True
        pixel_framebuf_led.fill(0xFF0000)
    elif temperatura_ambiente <= limite_temp_ambiente_min:
        fan_cooler.value = False
        pixel_framebuf_led.fill(0xFFFF00)
    elif (temperatura_ambiente >= limite_temp_ambiente_min) and (
        temperatura_ambiente <= limite_temp_ambiente_max
    ):
        pixel_framebuf_led.fill(0x00FF00)
    pixel_framebuf_led.display()

# Declaramos una funcion para mostrar texto por el display de Leds
def showText(text, colour):
    if len(str(text)) == 1:
        pixel_framebuf.text(str(text), 2, 0, colour)
        pixel_framebuf.display()
    else:
        for i in range(8, -6 * len(str(text)), -1):
            pixel_framebuf.fill(0)
            pixel_framebuf.text(str(text), i, 0, colour)
            pixel_framebuf.display()
            time.sleep(0.1)

# Declaramos una funcion para mostrar numeros por el display de Leds
def mostrarNumero(number, colour):
    if number in range(10) and type(number) == int:
        pixel_framebuf.text(str(number), 2, 0, colour)
        pixel_framebuf.display()
    else:
        for i in range(8, -6 * len(str(number)), -1):
            pixel_framebuf.fill(0)
            pixel_framebuf.text(str(number), i, 0, colour)
            pixel_framebuf.display()
            time.sleep(0.1)

# Declaramos una funcion para mostrar mensajes por el display de Leds
def mostrar_mensaje(texto, color, valor):
    global hora_inicio_luz, hora_apagado_luz, reloj, luz, porcentaje_humedad_suelo, limite_humedad_suelo_min, limite_humedad_suelo_max, bomba_agua_1, bomba_agua_2, bomba_agua_3, temperatura_ambiente, limite_temp_ambiente_max, limite_temp_ambiente_min, fan_cooler, limite_tem_ambiente_min, sensor_temp_humed_ambiente, humedad_suelo_min, humedad_suelo_max, sensor_humedad_suelo, humedad_ambiente
    showText(texto, color)
    mostrarNumero(valor, color)

# Declaramos una funcion para mostrar emojis por el display de Leds
def pintarEmoji(matriz, color):
    for i in range(len(matriz)):
        for j in range(len(matriz[i])):
            if matriz[i][j] == 1:
                pixel_framebuf.pixel(j, i, color)
    pixel_framebuf.display()

# Declaramos una funcion para gestionar la animacion (emojis)
def gestionar_animacion(
    temperatura_ambiente, limite_temp_ambiente_min, limite_temp_ambiente_max
):
    if temperatura_ambiente > limite_temp_ambiente_max:  # frio azul ma = 10 min= 2 2
        pintarEmoji(
            [
                [0, 0, 0, 0, 0, 0, 0, 0],
                [0, 0, 0, 0, 0, 0, 0, 0],
                [0, 0, 1, 0, 0, 1, 0, 0],
                [0, 0, 1, 0, 0, 1, 0, 0],
                [0, 0, 0, 0, 0, 0, 0, 0],
                [0, 0, 0, 0, 0, 0, 0, 0],
                [0, 1, 1, 1, 1, 1, 1, 0],
                [0, 0, 0, 0, 0, 0, 0, 0],
            ],
            0x0000FF,
        )
    elif temperatura_ambiente < limite_temp_ambiente_min:  # Archi se pone triste :(
        pintarEmoji(
            [
                [0, 0, 0, 0, 0, 0, 0, 0],
                [0, 0, 0, 0, 0, 0, 0, 0],
                [0, 0, 1, 0, 0, 1, 0, 0],
                [0, 0, 1, 0, 0, 1, 0, 0],
                [0, 0, 0, 0, 0, 0, 0, 0],
                [0, 0, 0, 0, 0, 0, 0, 0],
                [0, 0, 1, 1, 1, 1, 0, 0],
                [0, 1, 0, 0, 0, 0, 1, 0],
            ],
            0xFF0000,
        )
    else:
        pintarEmoji(
            [
                [0, 0, 0, 0, 0, 0, 0, 0],
                [0, 0, 0, 0, 0, 0, 0, 0],
                [0, 0, 1, 0, 0, 1, 0, 0],
                [0, 0, 1, 0, 0, 1, 0, 0],
                [0, 0, 0, 0, 0, 0, 0, 0],
                [0, 1, 0, 0, 0, 0, 1, 0],
                [0, 0, 1, 1, 1, 1, 0, 0],
                [0, 0, 0, 0, 0, 0, 0, 0],
            ],
            0x00FF00,
        )
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

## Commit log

2024-08-15 Subi los archivos de diseño en Altium
    [Archi_Farm_Beta.xlsx]
2024-08-15 Borre el Directorio
    [Archi_Farm_Beta.xlsx]
2024-08-15 Subi el Directorio Actualizado
    [Archi_Farm_Beta_BOM.xlsx]
2024-08-15 Subi archivos de codigo para ESP32, Archi y lib
2024-08-16 Se subio la carpeta img
2024-08-16 Se agrego imagen, por que github no soporta .HEIC
2024-08-16 se subio el video de timelapse
2024-08-16 Subi el TimeLapse.gif
2024-08-16 Se subio la Carpeta Documentos
2024-08-16 Se subieron los archivos de Diseño
    [Indoor archikids newsan.dxf]
2024-11-29 Delete Documentos/Indoor con ArchiFarmBeta.docx
    Se elimino el word con la espficificacion del modelo anterior del Farm
2024-11-29 Add files via upload
    Se agrego un pdf con la especificacion del Archi Farm nuevo
2024-11-29 Add files via upload
    Se agrega el procedimiento para lechugas en pdf. Se deja el word con el mismo contenido, para apreciar el TimeLapse
2024-11-29 Delete Documentos/Tutorial_Thingspeak.docx
    Se borra el archivo de word para ser reemplazado con un pdf
2024-11-29 Add files via upload
    Se agrega el tutorial de thingspeak en pedf
2024-11-29 Delete Hardware directory
    Se cambiara esta documentacion por la version actualizada de Archi Farm Beta
    [Archi_Farm_Beta_BOM.xlsx]
2024-11-29 Add files via upload
    Se agrega la nueva documentacion de Hardware para Archi Farm Beta
    [Archi_Farm_Beta.xlsx]
2024-11-29 Delete img/Archi_farm_beta_pines.jpg
    Se elimina esta version de AFB
2024-11-29 Add files via upload
    Se actualiza este pdf con la información del pinout de Archi Farm Beta
2024-11-29 Rename Sheet-ArchiFarmBeta.pdf to ArchiFarmBeta_Pinout.pdf
    Se cambia el nombre por uno mas adecuado
2024-11-29 Update README.md
    Se actualiza el pinout de AFB
2024-11-29 Add files via upload
    Se agrega la imagen del pinout para el readme
